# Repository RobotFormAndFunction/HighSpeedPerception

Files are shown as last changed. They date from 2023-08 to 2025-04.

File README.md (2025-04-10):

# HighSpeedPerception
Hardware and software for a high-speed vision-enabled microrobot

## Bill of Materials

|ID| Name	|Designator| Footprint |Quantity|	Manufacturer Part|	Manufacturer Supplier|	Supplier Part|	Price|
|--|--|--|--|--|--|--|--|--|
|1|	SEEDUINO_XIAO_ESP32C3 FLAT|	U3|	SEEDUINO_XIAO_ESP32C3|	1|||||				
|2|	10k|R1,R2,R4,R5|	R0402|	4|||||	
|3|	22p	|C1,C2	|C0603	|2|||||
|4|	0.1u|	C4	|C0603|	1|||||
|5|	2.2u|	C5|	C0603|	1|||||
|6|	10u|	C6|	C0603|	1|||||
|7|	10n|	C7|	C0603|	1|||||
|8|	1N4148WX|	D1|	SOD-323_L1.6-W1.3-LS2.7-RD|	1|	1N4148WX|	YONGYUTAI(永裕泰)|	LCSC|	C19089391|	0.009|
|9|	BNO055|	IMU|	LGA-28_L5.2-W3.8-P0.50-BL|	1	|BNO055	|Bosch(博世)|	LCSC|	C93216|	8.531||
|10|	Molex white 2-pin|	J1|	MOLEX PICOBLADE 2P SMD|	1|	Molex white 2-pin|||||		
|11|		|JP,R6,R10|	R0201|	3|||||					
|12|	10k|	R3|	R0603|	1|||||				
|13|	2355045-2|	U1|	HDR-TH_2P-P2.00-V-M|	1|	2355045-2|	TE Connectivity(美国泰科)|	LCSC|	C5439604|	0.516|
|14|	DRV8833CPWPR|	U2|	TSSOP-16_L5.0-W4.4-P0.65-LS6.4-BL-EP-1|	1|	DRV8833CPWPR|	Texas Instruments|	LCSC|	C191171|	0.713|
|15|	SM02B-SRSS-TB (LF)(SN)|U4,U6|	CONN-SMD_2P-P1.00_SM02B-SRSS-TB-LF-SN|	2	|SM02B-SRSS-TB(LF)(SN)|	JST	|LCSC	|C160402	|0.11|
|16|	32.768KHz|	XT	|CRYSTAL-SMD_L3.2-W1.5-FC-135R32.7680KF-A3	|1	|32.768Khz-SMD-3215	||LCSC	|C9900014196	||

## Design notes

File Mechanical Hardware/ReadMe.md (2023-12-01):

This folder contains the stl files for the chassis and the wheels.

The chassis (chassis.stl) and wheels (wheelmount_back.stl and wheel_mount_front.stl) are recommended to be printed on SLA printer with a hard resin. A FormLabs 3+ was used with the clear resin. The tires (wheel_tire.stl) is recommended to be printed with an elastic resin, or molded from an elastomeric material. A FormLabs 3+ was used with the elastic 50A resin. In total, one chassis is needed, two front wheels, two back wheels, and four tires.

The robot also needs two DC motors, two bearings, and carbon fiber rod to complete the build.

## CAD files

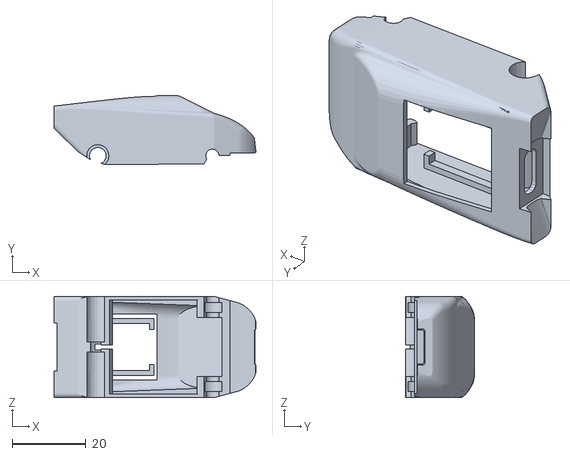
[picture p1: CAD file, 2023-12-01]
Mechanical Hardware/chassis.stl
54.8 x 18.7 x 27.5

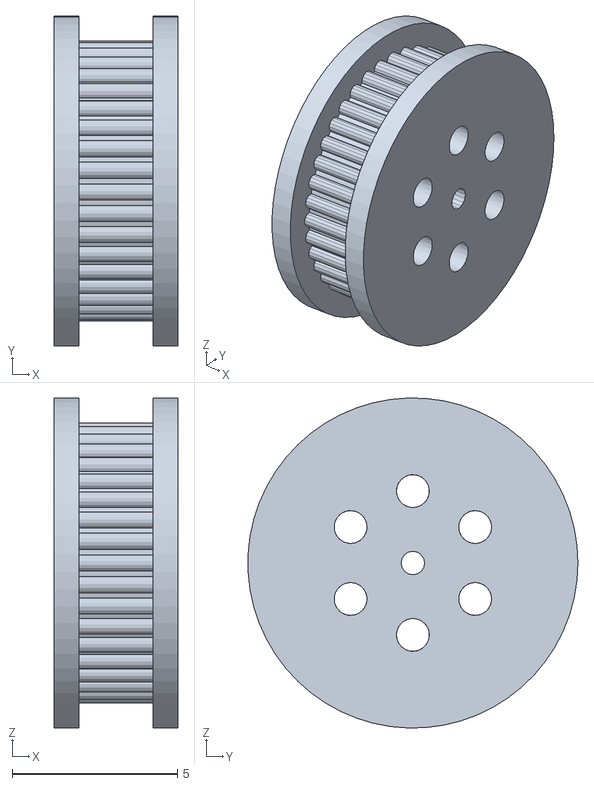
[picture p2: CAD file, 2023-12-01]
Mechanical Hardware/wheelmount_back.stl
3.75 x 9.99 x 10.00

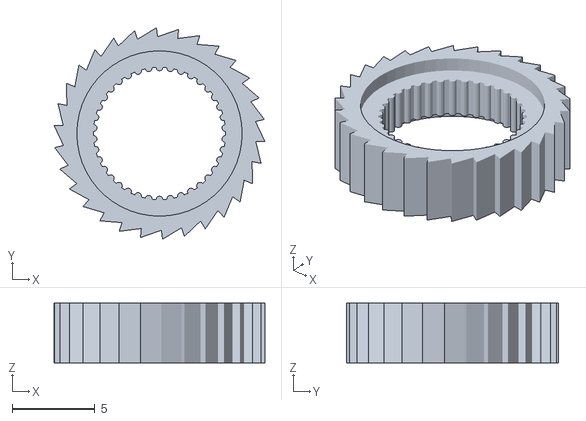
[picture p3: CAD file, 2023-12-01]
Mechanical Hardware/wheel_tire.stl
12.8 x 12.8 x 3.62

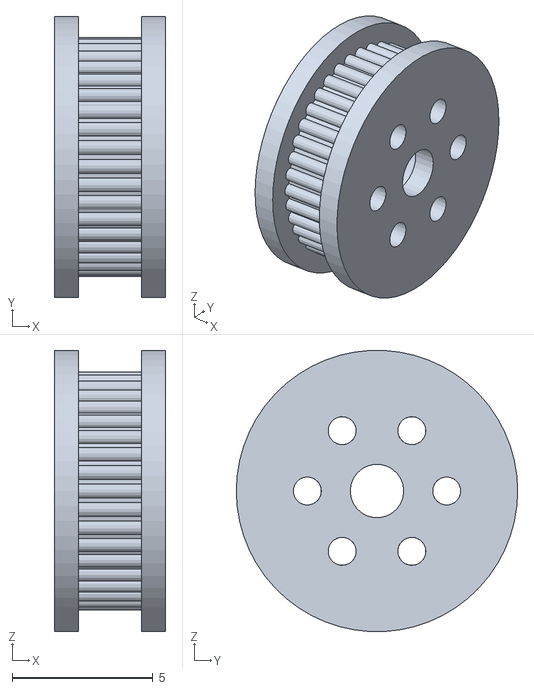
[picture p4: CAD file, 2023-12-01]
Mechanical Hardware/wheelmount_front.stl
3.95 x 10.0 x 9.99

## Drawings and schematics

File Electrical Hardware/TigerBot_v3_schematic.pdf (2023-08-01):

## ESP32 S3

## Battery connector and through holes for board

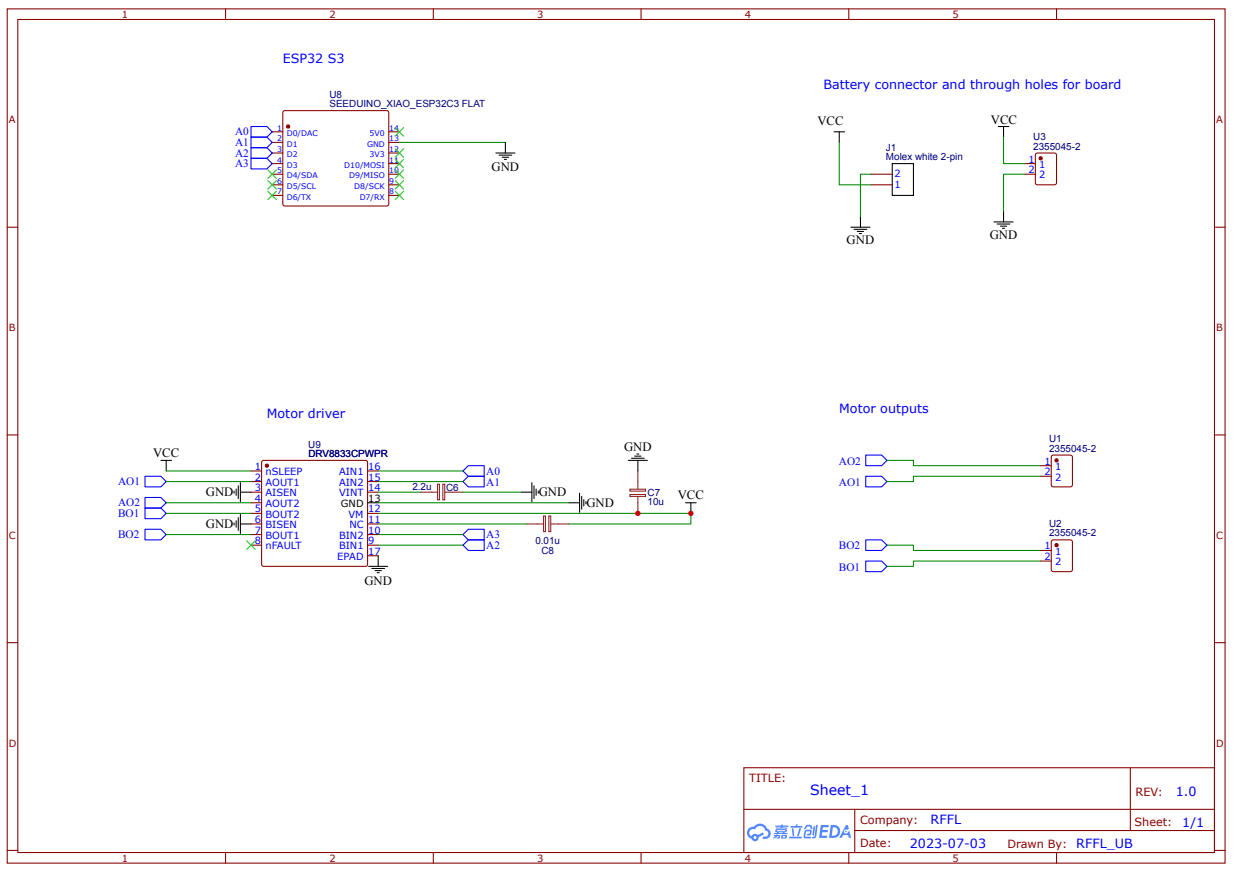
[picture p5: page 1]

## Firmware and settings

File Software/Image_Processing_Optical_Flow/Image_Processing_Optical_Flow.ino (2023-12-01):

#include "MatrixMath.h"
#include "esp_camera.h"
#include "soc/soc.h"           // Disable brownout problems
#include "soc/rtc_cntl_reg.h"  // Disable brownout problems
#include "driver/rtc_io.h"


#define CAMERA_MODEL_XIAO_ESP32S3 // Has PSRAM


//macro used to fill up an array with zeros
#define FILLARRAY(a, n) \
  do { \
    for (int _i = 0; _i < sizeof(a) / sizeof(a[0]); _i++) { \
      for (int _j = 0; _j < sizeof(a[0]) / sizeof(a[0][0]); _j++) { \
        a[_i][_j] = n; \
      } \
    } \
  } while (0)

#include "camera_pins.h"

const int IMAGE_WIDTH = 320; // set the camera properties to this size in the configure file
const int IMAGE_HEIGHT = 240; // set the camera properties to this size

// Two-dimensional array to hold the pixel values
uint8_t image2D[IMAGE_HEIGHT][IMAGE_WIDTH]; //two array to make a binary image file
uint8_t image2D_old[IMAGE_HEIGHT][IMAGE_WIDTH]; //two array to make a binary image file

// Declare 2D arrays for the x and y gradients
const int GRADIENT_WINDOW_HEIGHT = IMAGE_HEIGHT / 20;  // 5% of image height
const int GRADIENT_WINDOW_WIDTH = IMAGE_WIDTH;

// Declare 2D arrays for the x and y gradients
uint8_t Ix1[GRADIENT_WINDOW_HEIGHT][GRADIENT_WINDOW_WIDTH];
uint8_t Iy1[GRADIENT_WINDOW_HEIGHT][GRADIENT_WINDOW_WIDTH];
uint8_t It[GRADIENT_WINDOW_HEIGHT][GRADIENT_WINDOW_WIDTH];


const int windowSize = 3; //used for Lucas-Kanade optical flow algorithm
const int opticalFlowWindow = IMAGE_HEIGHT/20; //setting this up to only loo at at a 5% window in the middle

// Preallocate the optical flow vectors (2D arrays for each channel)
double flow_x[GRADIENT_WINDOW_HEIGHT][GRADIENT_WINDOW_WIDTH];
double flow_y[GRADIENT_WINDOW_HEIGHT][GRADIENT_WINDOW_WIDTH];

const int mat_row_size=(windowSize*2+1)*(windowSize*2+1);

double lambda = 1e-6;

mtx_type A[mat_row_size][2];
mtx_type At[2][mat_row_size];
mtx_type b[mat_row_size][1];
mtx_type AtA[2][2];
mtx_type PI_A[2][2];
mtx_type v[2][1];




void setup() {
  Serial.begin(115200);
  WRITE_PERI_REG(RTC_CNTL_BROWN_OUT_REG, 0); //disable brownout detector

  camera_config_t config; //setting up configuration 
  config.ledc_channel = LEDC_CHANNEL_0;
  config.ledc_timer = LEDC_TIMER_0;
  config.pin_d0 = Y2_GPIO_NUM;
  config.pin_d1 = Y3_GPIO_NUM;
  config.pin_d2 = Y4_GPIO_NUM;
  config.pin_d3 = Y5_GPIO_NUM;
  config.pin_d4 = Y6_GPIO_NUM;
  config.pin_d5 = Y7_GPIO_NUM;
  config.pin_d6 = Y8_GPIO_NUM;
  config.pin_d7 = Y9_GPIO_NUM;
  config.pin_xclk = XCLK_GPIO_NUM;
  config.pin_pclk = PCLK_GPIO_NUM;
  config.pin_vsync = VSYNC_GPIO_NUM;
  config.pin_href = HREF_GPIO_NUM;
  config.pin_sscb_sda = SIOD_GPIO_NUM;
  config.pin_sscb_scl = SIOC_GPIO_NUM;
  config.pin_pwdn = PWDN_GPIO_NUM;
  config.pin_reset = RESET_GPIO_NUM;
  config.xclk_freq_hz = 20000000;
  config.frame_size = FRAMESIZE_QVGA; //changed to qvga for (320 x 240)
  config.pixel_format = PIXFORMAT_GRAYSCALE; // changed to grayscale
  config.grab_mode = CAMERA_GRAB_WHEN_EMPTY;
  config.fb_location = CAMERA_FB_IN_PSRAM;
  config.jpeg_quality = 12; //this can be adjusted to create lower or higher quality images
  config.fb_count = 1;

  // camera initialize, will need to remove some of these things for the robot itself
  esp_err_t err = esp_camera_init(&config);

// set up two arrays for two images with 0s
  FILLARRAY(image2D, 0);
  FILLARRAY(image2D_old, 0);

}

void loop(){
  // setting up a pointer to the frame buffer
  camera_fb_t * fb = NULL;
  
  // Take Picture with camera and put in buffer
  fb = esp_camera_fb_get();

  // If something exists in the frame buffer, then put it in the two-d array
  if (fb) {
    // Transfer pixel data from the image buffer to the 2D array
    for (int row = 0; row < IMAGE_HEIGHT; row++) {
      for (int col = 0; col < IMAGE_WIDTH; col++) {
        int index = (row * IMAGE_WIDTH) + col; // Calculate the index in the 1D buffer
        image2D[row][col] = fb->buf[index];   // Copy the pixel value to the 2D array
      }
    }

  // Release the image buffer
  esp_camera_fb_return(fb);
  }

  // now to do optical flow between two images
  // First compute the spatial gradient of the old image
  computeGradient_oldimage();
  computeTimeGradient();
  computeOpticalFlow();

  // Store the new image as the old image
  for (int row = 0; row < IMAGE_HEIGHT; row++) {
    for (int col = 0; col < IMAGE_WIDTH; col++) {
      image2D_old[row][col] = image2D[row][col];
    }
  }

  //implement control based on flow_x
for(int i = 0; i < IMAGE_WIDTH; i++)
{
  Serial.print(flow_x[i][1]);
}
Serial.println(" ");

  
}



void computeGradient_oldimage() {
  // Compute gradients in the x and y directions within the optical flow window
  int y_start = IMAGE_HEIGHT/2 - GRADIENT_WINDOW_HEIGHT/2; // Start from 45% of the image height
  int y_end = IMAGE_HEIGHT/2 + GRADIENT_WINDOW_HEIGHT/2;   // End at 55% of the image height
  
  for (int y = y_start; y < y_end; y++) {
    for (int x = 0; x < IMAGE_WIDTH; x++) {
      // Calculate the x-gradient
      if (x == 0) {
        Ix1[y][x] = image2D_old[y][x + 1] - image2D_old[y][x]; // Forward difference
      } else if (x == IMAGE_WIDTH - 1) {
        Ix1[y][x] = image2D_old[y][x] - image2D_old[y][x - 1]; // Backward difference
      } else {
        Ix1[y][x] = (image2D_old[y][x + 1] - image2D_old[y][x - 1]) / 2; // Central difference
      }

      // Calculate the y-gradient
      if (y == y_start) {
        Iy1[y][x] = image2D_old[y + 1][x] - image2D_old[y][x]; // Forward difference
      } else if (y == y_end - 1) {
        Iy1[y][x] = image2D_old[y][x] - image2D_old[y - 1][x]; // Backward difference
      } else {
        Iy1[y][x] = (image2D_old[y + 1][x] - image2D_old[y - 1][x]) / 2; // Central difference
      }
    }
  }
}


void computeTimeGradient() {
  // Compute temporal gradient
  for (int y = IMAGE_HEIGHT/2 - GRADIENT_WINDOW_HEIGHT/2; y < IMAGE_HEIGHT/2 + GRADIENT_WINDOW_HEIGHT/2; y++) {
    for (int x = 0; x < IMAGE_WIDTH; x++) {
      int index = (y * IMAGE_WIDTH) + x;
      // Calculate the temporal gradient (difference between current and old frames)
      It[y][x] = image2D[y][x] - image2D_old[y][x];
    }
  }
}

//following Lucas-Kanade optical flow algorithm
void computeOpticalFlow(){
    int A_row = 0; //initial row counter
    // Compute the optical flow for each pixel
    for (int y = windowSize + 1; y < IMAGE_HEIGHT - windowSize; y++) {
        for (int x = windowSize + 1; x < IMAGE_WIDTH - windowSize; x++) {
            // Extract the window around the current pixel in both images
            int window_start_y = y - windowSize;
            int window_end_y = y + windowSize;
            int window_start_x = x - windowSize;
            int window_end_x = x + windowSize;

            // Fill the matrix A with gradient values and vector b with temporal gradient values
            for (int window_y = window_start_y; window_y <= window_end_y; window_y++) {
                for (int window_x = window_start_x; window_x <= window_end_x; window_x++) {
                    A[A_row][0] = Ix1[window_y][window_x];
                    A[A_row][1] = Iy1[window_y][window_x];
                    b[A_row][0] = -1*It[window_y][window_x];                 
                    A_row++;
                }
            }
            // Compute the Moore-Penrose pseudo-inverse of A with regularization this is matlab script that was translated A_pseudo_inverse = inv((A' * A + lambda * eye(size(A, 2)))) * A';
            Matrix.Transpose((mtx_type*)A, mat_row_size, 2, (mtx_type*)At);
            Matrix.Multiply((mtx_type*)At, (mtx_type*)A, mat_row_size, 2, mat_row_size, (mtx_type*)AtA);
        
            AtA[0][0] += lambda; //add regularization to avoid singularities
            AtA[1][1] += lambda;
            
            Matrix.Invert((mtx_type*)AtA, 2);
            Matrix.Multiply((mtx_type*)AtA, (mtx_type*)At, 2, 2, mat_row_size, (mtx_type*)PI_A);
            Matrix.Multiply((mtx_type*)PI_A, (mtx_type*)b, 2, mat_row_size, 2, (mtx_type*)v);

            // Store the optical flow vector components in the preallocated arrays
            flow_x[y][x] = v[0][0];
            flow_y[y][x] = v[1][0];
        }
    }
}

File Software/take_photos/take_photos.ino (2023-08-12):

#include "esp_camera.h"
#include "FS.h"
#include "SD.h"
#include "SPI.h"


#define CAMERA_MODEL_XIAO_ESP32S3 // Has PSRAM

#include "camera_pins.h"

unsigned long lastCaptureTime = 0; // Last shooting time
int imageCount = 1;                // File Counter
bool camera_sign = false;          // Check camera status
bool sd_sign = false;              // Check sd status

// Save pictures to SD card
void photo_save(const char * fileName) {
  // Take a photo
  camera_fb_t *fb = esp_camera_fb_get();
  if (!fb) {
    Serial.println("Failed to get camera frame buffer");
    return;
  }
  // Save photo to file
  writeFile(SD, fileName, fb->buf, fb->len);
  
  // Release image buffer
  esp_camera_fb_return(fb);

  Serial.println("Photo saved to file");
}

// SD card write file
void writeFile(fs::FS &fs, const char * path, uint8_t * data, size_t len){
    Serial.printf("Writing file: %s\n", path);

    File file = fs.open(path, FILE_WRITE);
    if(!file){
        Serial.println("Failed to open file for writing");
        return;
    }
    if(file.write(data, len) == len){
        Serial.println("File written");
    } else {
        Serial.println("Write failed");
    }
    file.close();
}


  
// define motor pins 
const int A_input_0 = D0;

const int A_input_1 = D1;

const int B_input_0 = D2;

const int B_input_1 = D3;


void setup() {

  // set mode of pins to be digital outputs 
  pinMode(A_input_0, OUTPUT);
  pinMode(A_input_1, OUTPUT);
  pinMode(B_input_0, OUTPUT);
  pinMode(B_input_1, OUTPUT);



  Serial.begin(115200);
  while(!Serial); // When the serial monitor is turned on, the program starts to execute

  camera_config_t config;
  config.ledc_channel = LEDC_CHANNEL_0;
  config.ledc_timer = LEDC_TIMER_0;
  config.pin_d0 = Y2_GPIO_NUM;
  config.pin_d1 = Y3_GPIO_NUM;
  config.pin_d2 = Y4_GPIO_NUM;
  config.pin_d3 = Y5_GPIO_NUM;
  config.pin_d4 = Y6_GPIO_NUM;
  config.pin_d5 = Y7_GPIO_NUM;
  config.pin_d6 = Y8_GPIO_NUM;
  config.pin_d7 = Y9_GPIO_NUM;
  config.pin_xclk = XCLK_GPIO_NUM;
  config.pin_pclk = PCLK_GPIO_NUM;
  config.pin_vsync = VSYNC_GPIO_NUM;
  config.pin_href = HREF_GPIO_NUM;
  config.pin_sscb_sda = SIOD_GPIO_NUM;
  config.pin_sscb_scl = SIOC_GPIO_NUM;
  config.pin_pwdn = PWDN_GPIO_NUM;
  config.pin_reset = RESET_GPIO_NUM;
  config.xclk_freq_hz = 20000000;
  config.frame_size = FRAMESIZE_UXGA;
  config.pixel_format = PIXFORMAT_JPEG; // for streaming
  config.grab_mode = CAMERA_GRAB_WHEN_EMPTY;
  config.fb_location = CAMERA_FB_IN_PSRAM;
  config.jpeg_quality = 12;
  config.fb_count = 1;
  
  // if PSRAM IC present, init with UXGA resolution and higher JPEG quality
  //                      for larger pre-allocated frame buffer.
  if(config.pixel_format == PIXFORMAT_JPEG){
    if(psramFound()){
      config.jpeg_quality = 10;
      config.fb_count = 2;
      config.grab_mode = CAMERA_GRAB_LATEST;
    } else {
      // Limit the frame size when PSRAM is not available
      config.frame_size = FRAMESIZE_SVGA;
      config.fb_location = CAMERA_FB_IN_DRAM;
    }
  } else {
    // Best option for face detection/recognition
    config.frame_size = FRAMESIZE_240X240;
#if CONFIG_IDF_TARGET_ESP32S3
    config.fb_count = 2;
#endif
  }

  // camera init
  esp_err_t err = esp_camera_init(&config);
  if (err != ESP_OK) {
    Serial.printf("Camera init failed with error 0x%x", err);
    return;
  }
  
  camera_sign = true; // Camera initialization check passes

  // Initialize SD card
  if(!SD.begin(21)){
    Serial.println("Card Mount Failed");
    return;
  }
  uint8_t cardType = SD.cardType();

  // Determine if the type of SD card is available
  if(cardType == CARD_NONE){
    Serial.println("No SD card attached");
    return;
  }

  Serial.print("SD Card Type: ");
  if(cardType == CARD_MMC){
    Serial.println("MMC");
  } else if(cardType == CARD_SD){
    Serial.println("SDSC");
  } else if(cardType == CARD_SDHC){
    Serial.println("SDHC");
  } else {
    Serial.println("UNKNOWN");
  }

  sd_sign = true; // sd initialization check passes

  Serial.println("Photos will begin in one second, please be ready.");


  




}

void loop() {
// added this block to test motor functionality
    digitalWrite(LED_BUILTIN,HIGH);

    digitalWrite(D0, HIGH);

    digitalWrite(D2, HIGH);

    digitalWrite(D1, LOW);

    digitalWrite(D3, LOW);

    delay(100);

    digitalWrite(LED_BUILTIN,LOW);

    delay(100);


  // Camera & SD available, start taking pictures
  if(camera_sign && sd_sign){
    // Get the current time
    unsigned long now = millis();
  
    //If it has been more than 1 minute since the last shot, take a picture and save it to the SD card
    if ((now - lastCaptureTime) >= 1000) {
      char filename[32];
      sprintf(filename, "/image%d.jpg", imageCount);
      photo_save(filename);
      Serial.printf("Saved picture：%s\n", filename);
      Serial.println("Photos will begin in one second, please be ready.");
      imageCount++;
      lastCaptureTime = now;
   
         digitalWrite(LED_BUILTIN,LOW);
    }
  }
}

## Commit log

2023-08-04 Add files via upload
    These are the most recent CAD models for specific elements of the TigerBot: the most recent casing, the rims for the front (carbon fiber rims) and back (coreless dc motor)
    [TigerBot V2 Casing v3.stl, TigerBot Wheel Rim v4.stl]
2023-08-04 Add files via upload
    This code (and the associated libraries) allows the robot to stream continuous data and send it to a web server in real-time. Currently, the code establishes all connections, but due to UB's strong w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
2023-08-04 reorganize folders
    [TigerBot V2 Casing v3.stl, TigerBot Wheel Rim v4.stl]
2023-12-01 update mechanical hardware
    [TigerBot V2 Casing v3.stl, TigerBot Wheel Rim v4.stl, chassis.stl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]
2024-12-05 Add files via upload
    this is an edited version of the CameraWebServer code that allows the ESP32-CAM to generate its own local network to host the server. In the loop section there is code to drive motors
2025-04-10 Update README.md
    added BOM (still needs some info)
